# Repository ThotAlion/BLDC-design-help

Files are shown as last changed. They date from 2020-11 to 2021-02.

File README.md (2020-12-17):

# Help to design BLDC articulations
BLDC controllers are very new with respect the classical DC motor controllers, mainly taking into account position control. The objective of this repo is to gather studies to help design of robots (small and big) with BLDC.

## STL files

Find in this Repo the STL Files used to test the two motors. Find also STL files for the USB-CAN Box for the Tinymovr kit.

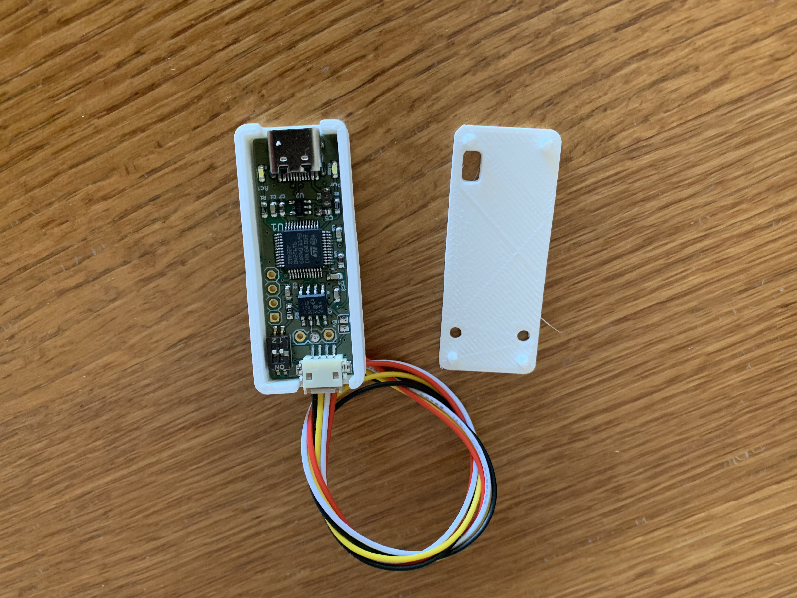
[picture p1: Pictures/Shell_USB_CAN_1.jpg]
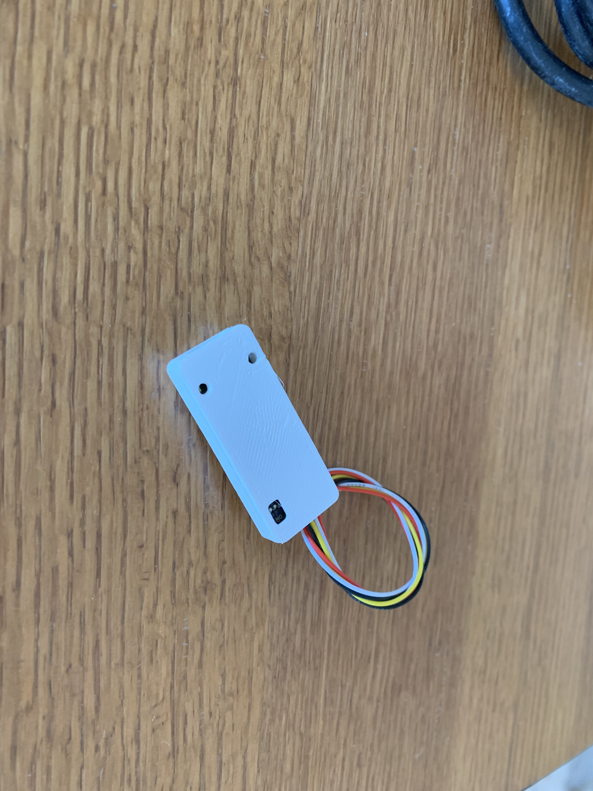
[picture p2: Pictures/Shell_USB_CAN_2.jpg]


## Motors

| |Motor 1 |Motor 2|
| --- |:---:|:-----:|
|Picture||MAD|
| Ref| [Eachine  2204-2300KV](https://www.eachine.com/Eachine-Racer-250-Drone-Spare-Part-BG2204-2300KV-Brushless-Motor-CW-or-CCW-p-343.html)|[MAD component 5005-280KV](https://mad-motor.com/product/mad-5005-eee/)|
|Resistance/phase(milliOhms)|170|100|
|Inductance/phase(microHenri)|10|76|
|Outer diameter(mm)|28|56|
|Max quadratic current Iq in coils|12 A|18 A|
|Purpose|Fast/silent animatronics (eye)|Powerful robotic articulation|

-----
## Tinymovr controller

[Documentation](https://tinymovr.readthedocs.io/en/latest/)
Here, the tinymovr controller board is powered by a DC power supply 15V - 10A.
The communication is done via a standard FTDI USB - UART device (for experiment purpose here... Later via CAN bus)
By default, Iq is limited to 10A and speed to 300000ticks/s
1 turn is 8192 ticks.

-----
## Theory about BLDC

### The motor current

Iq = (Ia/sqrt(3) + 2*Ib/sqrt(3))*cos(theta) - Ia*sin(theta)

### The torque constant

Torque (N.m) = Kc*Iq(A)

### The speed constant

U(V) = Kv*Omega(rad/s)

Knowing that Kc = 1/Kv

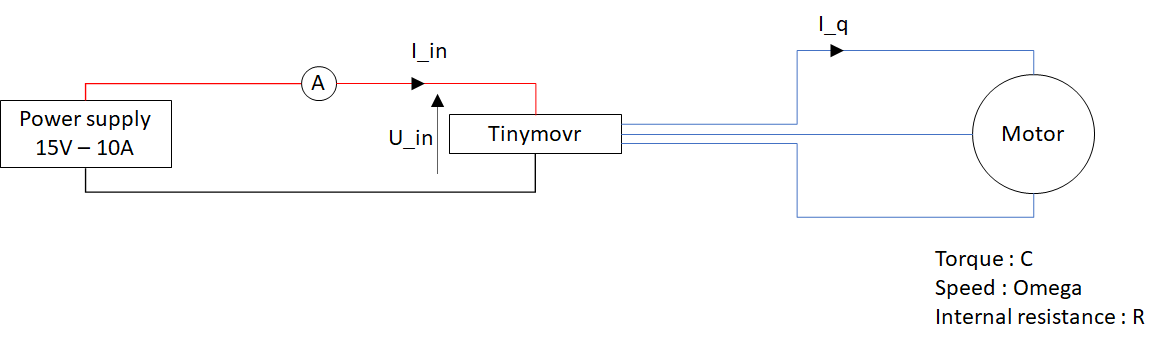
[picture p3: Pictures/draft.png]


The power in the system is used in internal resistor, controller and to general mechanical movement

P_in = P_Joule + P_controller + P_mecha

P_in = U_in.I_in = I_q.I_q.R + P_controller + C*Omega

P_controller in control state is here 0.060A for 15V => 1W

To get the input current when motor is blocked (consider power of controller is small enough) :

I_in = R.I_q.I_q/U_in

-----

### A small motor (2204-2300KV) + Tinymovr controller - push test

the motor is set next to a weighing scale with a lever arm of 95mm. 
Input voltage : 15V.

#### Measures

| Position target (ticks)| Motor current Iq (A)| Input current Iinput (A)| weight (g)|torque (N.m)|
| --- |:---:| ---:|---:|---:|
| 0 | 0.918 | 0.060 |0 |0.000 |
| 1000 | -0.165 | 0.060 |5 |0.005 |
| 2000 | -3.640 | 0.120 |13 |0.012 |
| 3000 | -6.112 | 0.230 |21 |0.020 |
| 4000 | -8.710 | 0.420 |29 |0.028 |
| 5000 | -10.040 | 0.570 |34 |0.032 |

Find below the input current of the Tinymovr controller function of the current delivered in coils.

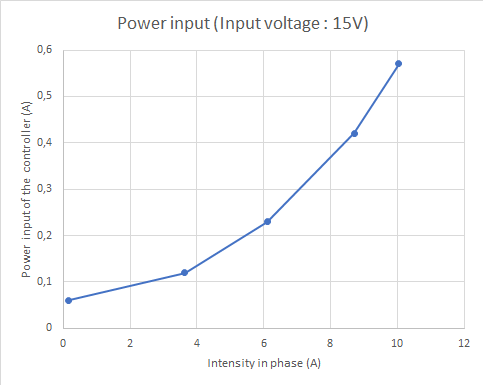
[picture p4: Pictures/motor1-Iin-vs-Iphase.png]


Find below the torque generated by the motor function of the current delivered in coils

Kc = Torque/Iphase = 0.032/10.04 = 0.0032 N.m/A

Kv = 1/Kc = 310.8 rad/s/V

KV = 2970 rpm/V

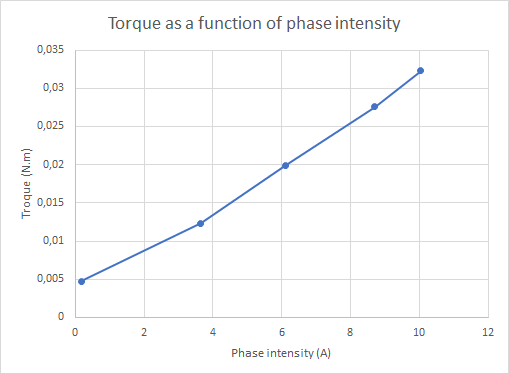
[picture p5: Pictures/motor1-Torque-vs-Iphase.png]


And find below the torque produced function of input current

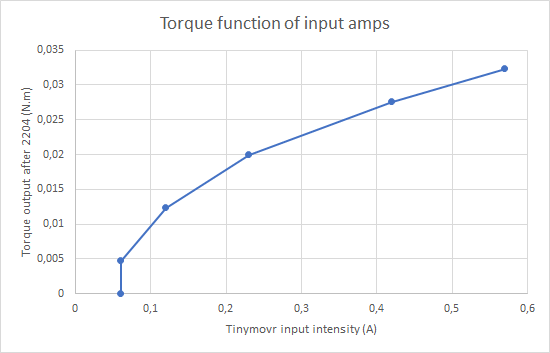
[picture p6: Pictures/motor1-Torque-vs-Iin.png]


### A bigger motor (5005-280KV) + Tinymovr controller - push test

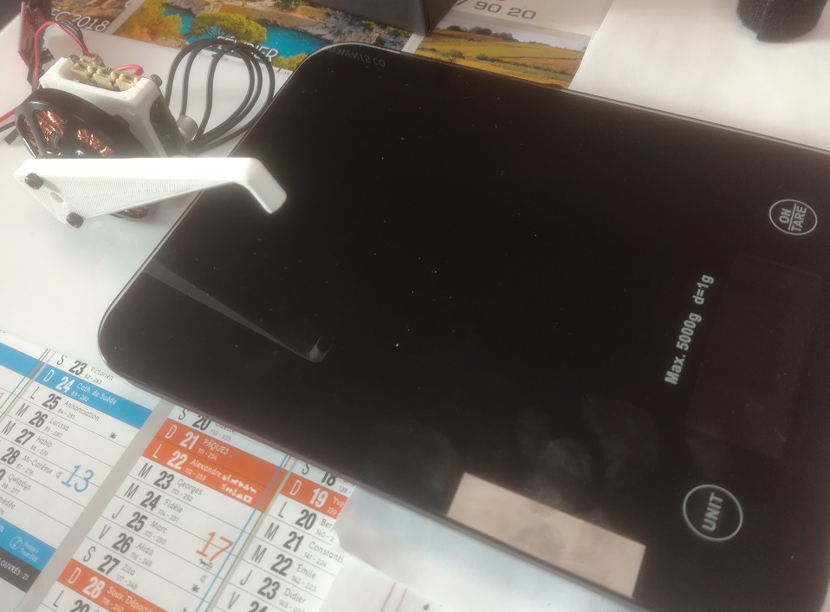
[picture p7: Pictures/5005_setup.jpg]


the motor is set next to a weighing scale with a lever arm of 98mm. 
Input voltage : 15V.

#### Measures

| Position target (ticks)| Motor current Iq (A)| Input current Iinput (A)| weight (g)|torque (N.m)|
| --- |:---:| ---:|---:|---:|
| 0 | 0.277 | 0.050 |0 |0.000 |
| 1000 | -1.983 | 0.090 |50 |0.048 |
| 2000 | -4.547 | 0.200 |112 |0.106 |
| 3000 | -6.995 | 0.420 |175 |0.166 |
| 4000 | -9.527 | 0.740 |236 |0.224 |
| 5000 | -9.973 | 0.840 |247 |0.235 |
| 6000 | -10.025 | 0.860 |249 |0.237 |

Find below the input current of the Tinymovr controller function of the current delivered in coils.

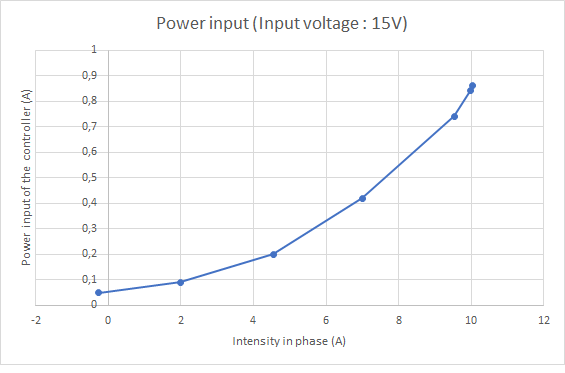
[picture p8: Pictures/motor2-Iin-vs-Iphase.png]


Find below the torque generated by the motor function of the current delivered in coils

Kc = Torque/Iphase = 0.032/10.04 = 0.0234 N.m/A

Kv = 1/Kc = 42.7 rad/s/V

KV = 407 rpm/V

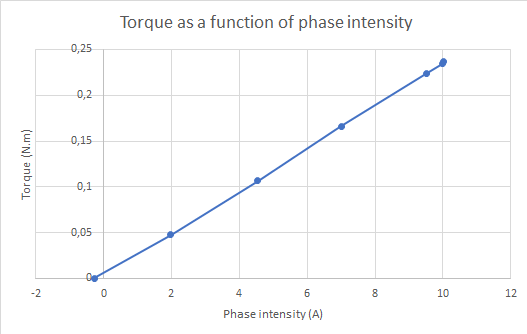
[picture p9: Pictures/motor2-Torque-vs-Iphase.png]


And find below the torque produced function of input current

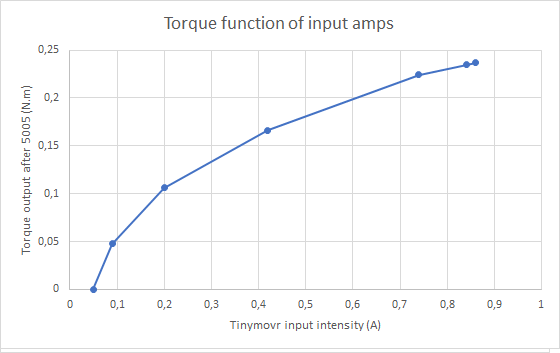
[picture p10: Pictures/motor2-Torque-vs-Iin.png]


----

### A small motor (2204-2300KV) + Tinymovr controller - speed test

the motor is without load

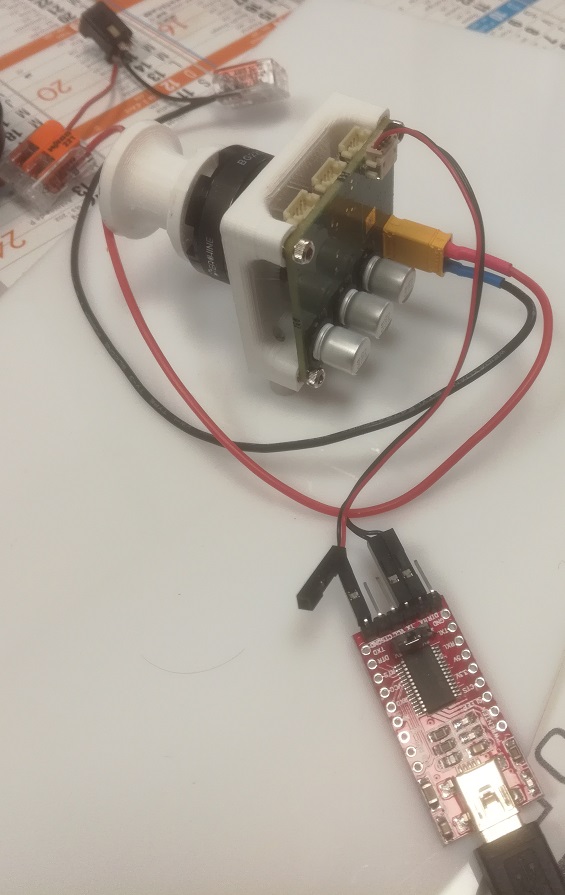
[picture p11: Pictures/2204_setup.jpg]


| Speed target (ticks/s)| Input amps (A)| Measured speed (ticks/s)|
| --- |:---:| ---:|
| 0 | 0.060 | 168 |
| 7000 | 0.060 | 506 |
| 8000 | 0.060 | 2373 |
| 10000 | 0.060 | 9880 |
| 20000 | 0.060 | 17605 |
| 40000 | 0.060 | 38343 |
| 80000 | 0.060 | 79606 |
| 160000 | 0.070 | 147904 |
| 320000 | 0.080 | 278386 |
| 640000 | 0.090 | 281503 |

See that until 10000 ticks/s, the measured speed is far from the commanded one. The rotor slips and is too slow.
On the contrary, the high speed does not go above 300000 ticks/s. This is nominal since the speed is limited (can be tuned in Tinymovr)

### A bigger motor (2204-2300KV) + Tinymovr controller - speed test

the motor is without load

| Speed target (ticks/s)| Input amps (A)| Measured speed (ticks/s)|
| --- |:---:| ---:|
| 0 | 0.060 | -0 |
| 5000 | 0.060 | -292 |
| 6000 | 0.060 | 4173 |
| 7000 | 0.060 | 4915 |
| 8000 | 0.060 | 5408 |
| 9000 | 0.060 | 7836 |
| 10000 | 0.060 | 8835 |
| 20000 | 0.090 | 75905 |
| 160000 | 0.140 | 166808 |
| 320000 | 0.470 | 270000 |

See that the motor can reach slower speeds even if it slips.

### Reactivity tests with a LeapMotion

This part is in progress, waiting for CAN controllers. Here is a small video with serial communication. The position gain is small by default, that is why, the phase inversion occurs at a very low frequency (with respect to a classical DC controller like Dynamixel)
The code is in this Repo (Leap2BLDCUART folder)

(https://www.youtube.com/watch?v=h77mSkhAOiY)

### Motor control with pygame

The folder MotorControl contains a Python3 script to control a brushless motor with a Tinymovr controller. Change the name of the serial port in the script before starting.

The key hacks are :
- Up arrow : hold position
- right arrow : decrease and hold position
- left arrow : increase and hold position
- z : set current position as zero
- c : calibrate
- r : reset the controller
- p : oscillate position between max and min current
- space : soft emergency stop

### With a belt reductor

The belt reductor design is under progress, based on [Open Dynamic Robot Initiative](https://github.com/open-dynamic-robot-initiative)

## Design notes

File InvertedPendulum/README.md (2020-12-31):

# Torque limited actuated inverted pendulum
BLDC controlled by a Tinymovr controller allows to build and experiment a "classical control problem" such as the inverted pendulum. Most of time, it is done in simulation but we cannot "play with it". Such a motor can perform in torque control with a relatively high torque (with respect to classical DC brushed motor). The fact the torque is controlled using current control is also useful since the current is "limited by design" and it will be difficult to exceed a maximum current. The risk of big melting motor is prevented.

There are several setups for inverted pendulums such as cart-pole. Here, the setup is to fix the pendulum directly on the rotor of the brushless motor. But we limit the torque such as it is not possible to lift directly the pendulum to set it upright.

(https://www.youtube.com/watch?v=rv7isctR4a8)

The motor chosen here is a 2204 at 2300KV (about 10$) found in our old shielves, piloted by the high tech Tinymovr controller with CANable interface. The max current of such a motor is 15Amps which is below the maximal allowed current by Tinymovr. The advantage of Tinymovr is the integrated absolute magnetic encoder and the CANable robust and fast interface.

Therefore, this dynamical control test setup is very cheap and easy to make. The but control theory needed in the background is advanced.

We advise to follow the underactuated robotics course of Russ Tedrake 

Russ Tedrake. Underactuated Robotics: Algorithms for Walking, Running, Swimming, Flying, and Manipulation (Course Notes for MIT 6.832). Downloaded on december 2020 from http://underactuated.mit.edu/

This test bench jumps directly [here](http://underactuated.mit.edu/pend.html#section3)

## Software setup

The Python script runs Python 3 using :
- pygame for keyboard real-time control and display
- tinymovr official library
- numpy

The setup here is for an Ubuntu 18 WSL under Windows 10 with [VcXsrv X Server](http://vcxsrv.sourceforge.net)

Line 36, the channel, if your CANable USB interface is on port COM6, the Ubuntu 18 WSL will see it on /dev/ttyS6

## Python structure

This script is of course not an "industrial" one but the objective is to be very short and with few functions. The structure is a classical for real-time test bench :

- Introduction to instanciate all variables and interfaces
- Open an infinite loop at 100Hz
- Get all sensors  (including keyboard inputs)
- running a finite state machine (including safety conditions)
- running a control loop (here all is done inside Tinymovr board)
- send orders (including screen display)

There is only one parameter linked to the mechanical structure of the pendulum, its natural frequency w0. To get it, measure the period of the pendulum by making several swings during one minute. Type it in line 25.

The finite state machine has 4 states :
- 0 : the safety state with current controlled to 0Amps. This state is set each time a key is released (dead man safety)
- 1 : the damping state with velocity controlled to zero. Just push down arrow to damp the pendulum. In some seconds, the pendulum is stopped. (press down arrow)
- 2 : the most "exotic" state with mechanical energy control. the nrj variable is proportionnal to the total mechanical energy of the pendulum, the sum of potential energy and kinetic energy. Without any torque of air damping, this energy must be conserved. In this mode, the energy is controlled to reach nrj0, the energy of the still upright pendulum. (press space bar)
- 3 : Upright proportional controller. When the pendulum is close to the upright position with a relatively small speed, it is possible to control the pendulum upright very easily using internal Tinymovr control loop. (press up arrow)

Notice states 2 and 3 can switch between them, the condition is to be "almost upright".

You can leave the program by pressing ESC or click the right upper cross.

Press the "z" key to reset the zero of the pendulum (down)

Press the "r" key to hard reset the Tinymovr (the program will also be killed)

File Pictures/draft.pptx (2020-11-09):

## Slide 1

I_in

I_q

Power supply 15V – 10A

A

U_in

Tinymovr

Motor

Torque : C
Speed : Omega
Internal resistance : R

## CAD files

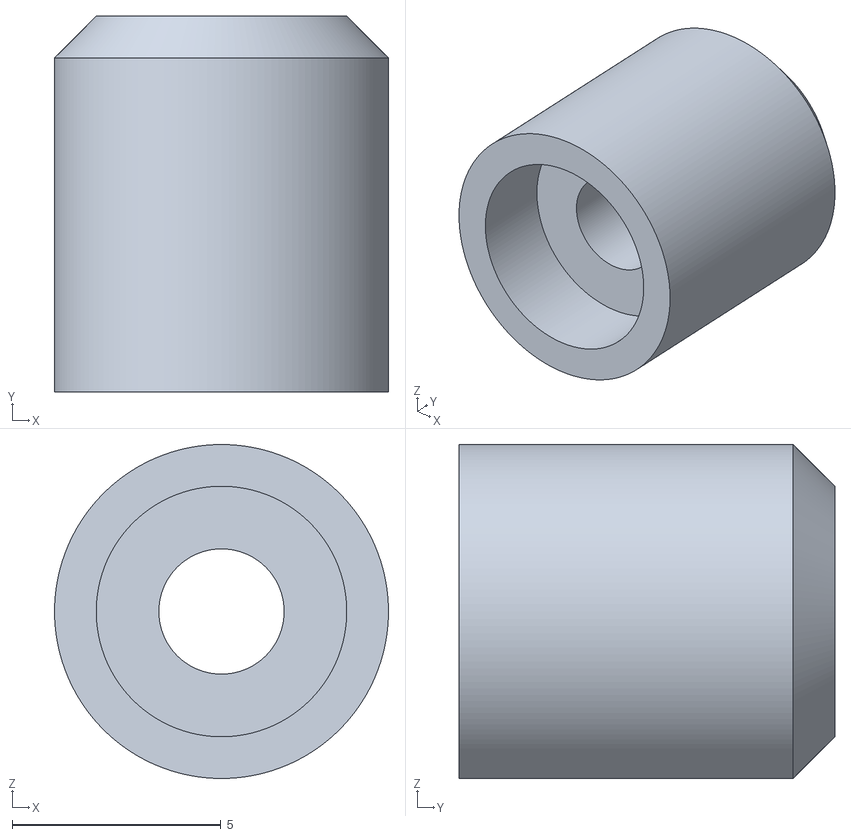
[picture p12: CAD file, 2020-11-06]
STL/testBench/BG2204-Magnet.stl
8.00 x 9.00 x 8.00

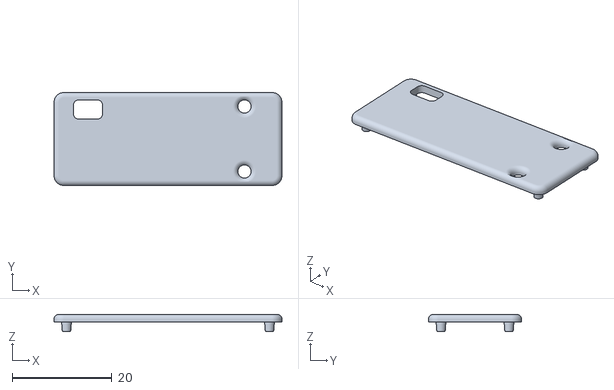
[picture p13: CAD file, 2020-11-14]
STL/USBCANBox/USB_CAN_Cover.stl
45.6 x 18.6 x 3.50

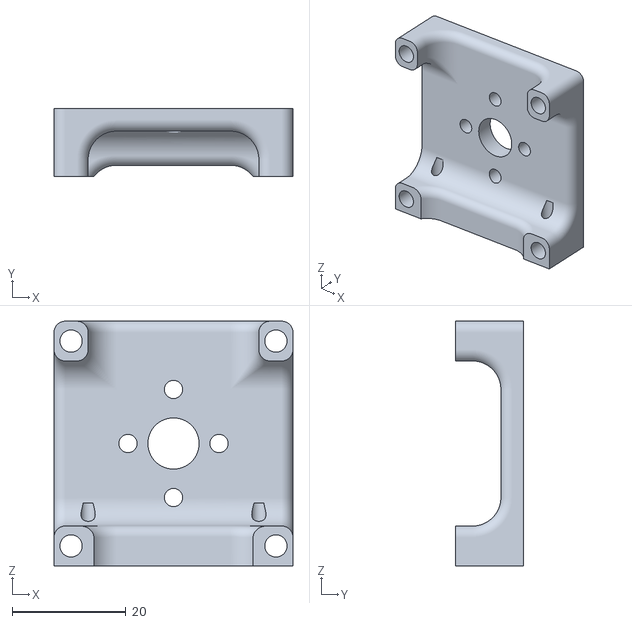
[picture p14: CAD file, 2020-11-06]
STL/testBench/BG2204-Plate.stl
42.0 x 12.0 x 43.0

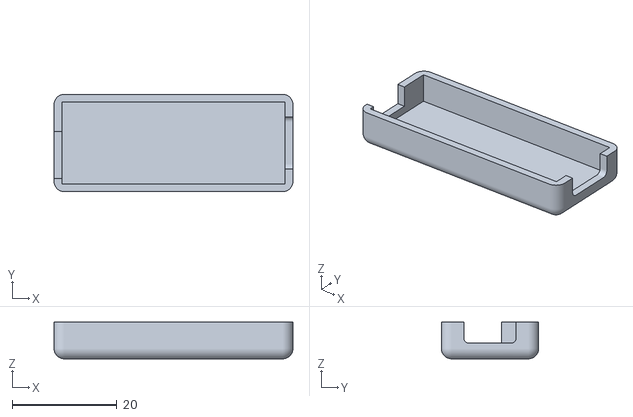
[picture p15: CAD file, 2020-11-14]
STL/USBCANBox/USB_CAN_Shell.stl
45.6 x 18.6 x 7.00

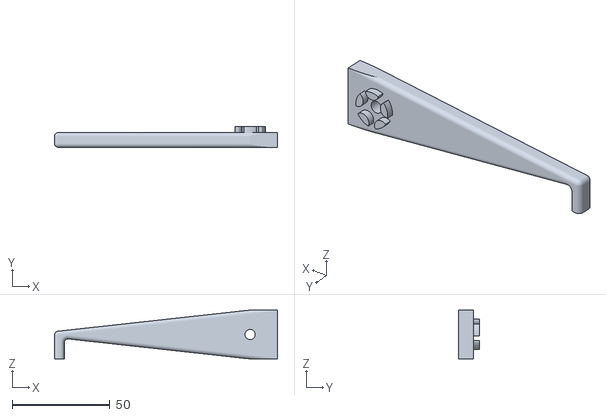
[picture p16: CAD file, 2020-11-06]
STL/testBench/BG2204-Lever-Arm.stl
114.0 x 10.6 x 25.0

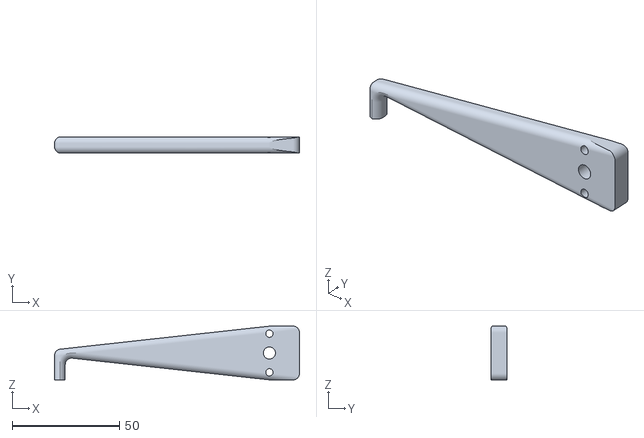
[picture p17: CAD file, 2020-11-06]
STL/testBench/MAD5005-Lever-Arm.stl
114.0 x 7.60 x 25.0

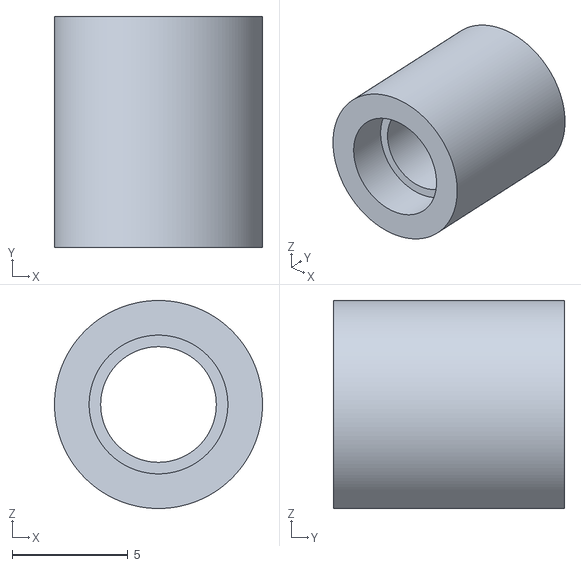
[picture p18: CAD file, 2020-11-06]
STL/testBench/MAD5005-Magnet.stl
9.00 x 10.0 x 9.00

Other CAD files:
STL/testBench/MAD5005-Plate.stl

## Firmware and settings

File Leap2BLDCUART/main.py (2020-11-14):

# this simple code connects a leap motion to Tinymovr controller
# Window code

import time, json,os
import Leap
import random
from numpy import *
import serial

# sampling rate (s)
dt = 0.01
# index yaw angle (along x-axis of the leap motion)
z = 0.0
# flag to notify if there is a hand
isFinger = False
# ID of the COM port
port = "COM5"

# instanciate Leap Motion and Serial Port
ser = serial.Serial(port, 115200, timeout=0.005)
leapController = Leap.Controller()

# calibrate the motor
time.sleep(1)
print(".Q")
ser.write(".Q\n")
time.sleep(10)

# activate the closed loop
print(".A")
ser.write(".A\n")

while True:
    # get the sensors
    # time
    t = time.clock()
    # leap
    isFinger = False
    frame = leapController.frame()
    for fin in frame.fingers:
        if fin.hand.is_left and fin.type == fin.TYPE_INDEX:
            z = int(2*4096*fin.direction.x/pi)
            isFinger = True

    # send the command
    if isFinger:
        ser.write(".P"+str(z)+"\n")
        print(z)
    else:
        ser.write(".I0\n")

    # wait approximately until the next top
    time.sleep(dt)

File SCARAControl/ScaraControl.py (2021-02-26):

from numpy import *
import pygame
import time
import can
from tinymovr import Tinymovr
from tinymovr.iface.can import CAN, guess_channel
from tinymovr.units import get_registry
# Definition of units
ureg = get_registry()
Q_ = ureg.Quantity
A = ureg.ampere
s = ureg.second
min = ureg.minute
rad = ureg.radian
deg = ureg.degree
m = ureg.meter
turn = ureg.turn
degC = ureg.degC


pygame.init()
ecran = pygame.display.set_mode((800, 400))
font = pygame.font.SysFont(None, 48)

# geometry
# Knee
ratioKnee = abs((1145-(-573)))/180.0 #9.54
# Thigh
ratioThigh = abs((-827-(881)))/180.0 #9.48
# geometry of the leg
L1 = 0.18025*m
L2 = 0.16005*m
LMAX = L1+L2

# sampling period (s)
dt = 0.001
goon = True
step=1*deg
theta1 = 0*deg
theta2 = 0*deg
theta10 = 0*deg
theta20 = 0*deg
t0 = 0
Y0= 0.0*m
Z0= 0.0*m
alpha = 0.0*deg
D = 0.0*m
E = 0.0*m
F = 0.0*m
Yfoot = 0.0*m
Zfoot = (L1+L2)*m
modepygame = -1




# channel = guess_channel(bustype_hint='slcan')
channel='/dev/ttyS7'
can_bus = can.Bus(bustype='slcan',channel=channel,bitrate=1000000)
iface = CAN(can_bus)
tm1 = Tinymovr(node_id=2, iface=iface)
tm2 = Tinymovr(node_id=1, iface=iface)

maxspeed = 1500*turn/min
tm1.set_limits(velocity=maxspeed*1.5, current=22.0*A)
tm2.set_limits(velocity=maxspeed, current=22.0*A)
tm1.set_gains(position=100.0, velocity=0.0002)
tm2.set_gains(position=100.0, velocity=0.0002)
tm1.set_integrator_gains(velocity=0.001)
tm2.set_integrator_gains(velocity=0.001)

# print(tm1.motor_info)
# print(tm2.motor_info)
# print(tm1.device_info)
# print(tm2.device_info)
jump = 0.08

while goon:
    tr0 = time.time()
    # sensors
    # keyboard
    for event in pygame.event.get():
        if event.type == pygame.QUIT:
            goon = False
        elif event.type == pygame.KEYDOWN:
            if event.key == pygame.K_ESCAPE:
                goon = False
            elif event.key == pygame.K_DOWN and modepygame == 0:
                print ("bas")
                modepygame = 3
            elif event.key == pygame.K_UP and modepygame == 0:
                print ("haut")
                modepygame = 2
            elif event.key == pygame.K_LEFT and modepygame == 0:
                print ("gauche")
                modepygame = 4
            elif event.key == pygame.K_RIGHT and modepygame == 0:
                print ("droite")
                modepygame = 5
            elif event.key == pygame.K_SPACE:
                print ("space")
                modepygame = -2
            elif event.key == pygame.K_z:
                print ("ZERO")
                theta10 = tm1.encoder_estimates.position
                theta20 = tm2.encoder_estimates.position
                t0 = time.time()
                Y0 = 0.0*m
                Z0 = -L1-L2
                modepygame = 0
            elif event.key == pygame.K_p and modepygame == 0:
                print ("POINT")
                modepygame = 1
            elif event.key == pygame.K_o and modepygame == 0:
                print ("HAUTBAS")
                modepygame = 6
            elif event.key == pygame.K_a:
                print ("Step+")
                step+=1.0*deg
                step=minimum(step,100*deg)
                print(step)
            elif event.key == pygame.K_q:
                print ("Step-")
                step-=1.0*deg
                step=maximum(step,-100*deg)
                print(step)
            elif event.key == pygame.K_s:
                print ("STAY")
                modepygame = 0
            elif event.key == pygame.K_b:
                print ("p2p")
                modepygame = 7
                t0 = time.time()
                Y0= Y
                Z0= Z

                
        elif event.type == pygame.KEYUP:
            if modepygame == -2:
                modepygame = -2
            else:
                modepygame = 0
                t0 = time.time()
                Y0= Y
                Z0= Z

    # motors
    theta1m = (-tm1.encoder_estimates.position.to(deg)+theta10)/ratioThigh
    theta2m = (tm2.encoder_estimates.position.to(deg)-theta20)/ratioKnee
    Y = L1*sin(theta1m)+L2*sin(theta1m+theta2m)
    Z = -L1*cos(theta1m)-L2*cos(theta1m+theta2m)
    # print("theta1m,theta2m:"+str(theta1m.to(deg))+','+str(theta2m.to(deg)))
    # print("Y,Z:"+str(Y)+','+str(Z))

    

    # Finite state machine
    if modepygame == -1:
        print("CALM DOWN, CALIBRATE FIRST!")
        activated = False
        p2pactivated = False
    elif modepygame == -2:
        activated = False
        p2pactivated = False
    elif modepygame == 0:
        # activated = True
        # p2pactivated = False
        # alpha = 0.0*deg
        # E=0.0*m
        # F=-LMAX
        # D=0.0*m
        activated = False
        p2pactivated = True
        Yobj=0.0
        Zobj= -1.0*LMAX
        Duration = 5.0
    elif modepygame == 1:
        activated = True
        p2pactivated = False
        alpha = 0.0*deg
        E=0.0*m
        F=-0.7*(L1+L2)
        D=0.0*m
    elif modepygame == 2:
        activated = True
        p2pactivated = False
        alpha = +90.0*deg
        E=jump*m
        F=-1.0*(L1+L2)
        D=jump*m
    elif modepygame == 3:
        activated = True
        p2pactivated = False
        alpha = -90.0*deg
        E=jump*m
        F=-1.0*(L1+L2)
        D=jump*m
    elif modepygame == 4:
        activated = True
        p2pactivated = False
        alpha = 0.0*deg
        E=jump*m
        F=-1.0*(L1+L2)
        D=jump*m
    elif modepygame == 5:
        activated = True
        p2pactivated = False
        alpha = 180.0*deg
        E=jump*m
        F=-1.0*(L1+L2)
        D=jump*m
    elif modepygame == 6:
        activated = True
        p2pactivated = False
        alpha += step
        E=0.05*m
        F=-0.7*(L1+L2)
        D=0.04*m
    elif modepygame == 7:
        activated = False
        p2pactivated = True
        Yobj=0.0
        Zobj= - 0.3*LMAX
        Duration = 5.0


    if p2pactivated:
        # Control
        bary = maximum(0,minimum((time.time()-t0)/Duration,1))
        # print("bary: "+str(bary))
        Yfoot = Y0*(1-bary)+Yobj*bary
        Zfoot = Z0*(1-bary)+Zobj*bary
        
        # foot trajectory
        # Yfoot = E*cos(alpha)
        # Zfoot = F+D*sin(alpha)
        # print("YFoot,Zfoot: ("+str(Yfoot)+','+str(Zfoot)+")")

        # lenght and angle of leg
        L = sqrt(Yfoot**2+Zfoot**2)
        L = maximum(minimum(L,LMAX*1.0),LMAX*0.3)
        # print("L: "+str(L))
        theta = arcsin(Yfoot/L)
        theta = maximum(minimum(theta,45*deg),-45*deg)
        # print("L,theta: ("+str(L)+','+str(theta.to(deg))+")")
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

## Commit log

2020-11-05 corrections about Iq and current
2020-11-06 STL parts added
    [BG2204-Lever-Arm.stl, BG2204-Magnet.stl, BG2204-Plate.stl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]
2020-11-14 Add LeapMotion control via UART
2020-11-14 STL files for test bench
    [BG2204-Lever-Arm.stl, BG2204-Magnet.stl, BG2204-Plate.stl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]
2020-11-14 Add STL files for USB2CAN box
    [USB_CAN_Cover.stl, USB_CAN_Shell.stl]
2020-12-31 Document the inverted pendulum test bench
    [TorqueLimitedPendulum.py]
